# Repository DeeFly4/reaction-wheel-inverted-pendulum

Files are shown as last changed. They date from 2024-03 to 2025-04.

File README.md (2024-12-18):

# Reaction wheel inverted pendulum

This repository contains the code, schematics and the report for a school project course in Control Systems. The design, implementation and tuning of the controller was done by me with Arduino code. Much of the other parts of the project was handled by others in the group including design and creation of the physical parts as well as simulations in Matlab.

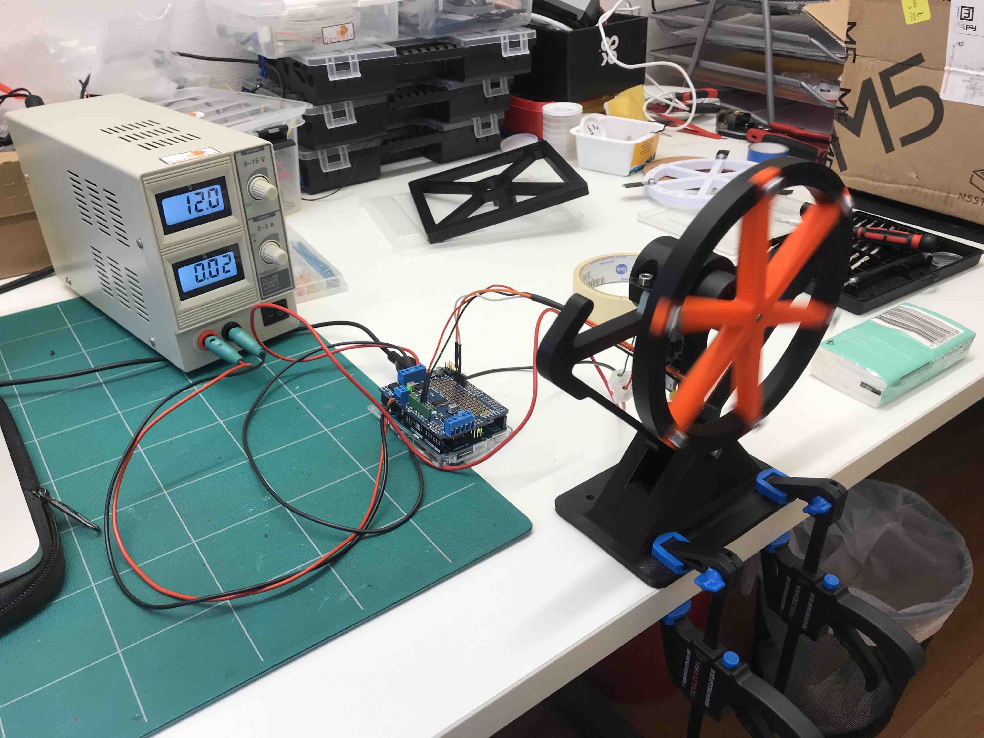
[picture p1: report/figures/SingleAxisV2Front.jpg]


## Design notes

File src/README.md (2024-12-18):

# Requirements
Both projects are Arduino code using PlatformIO. It can not be run through the standard Arduino IDE. Instead you will need to use Microsoft's Visual Studio Code with the PlatformIO extension.

## PlatformIO
1. Open VSCode Extension Manager
2. Search for offical PlatformIO IDE extension
3. Install PlatformIO IDE

For further info on PlatformIO, go to their website https://platformio.org/

# Running the code
Open either PlatformIO project, balance or imu, in a separate window. This will build the project locally to make sure all dependencies are installed according to the project's platformio.ini file. The standard Arduino code with setup() and loop() functions will be located in the files called main.cpp. In these files you will find further instructions to make sure the wiring is correct. Make sure to also follow the instructions in the serial monitor to start the program correctly.

The project must then be uploaded to the Arduino. This can be done by pressing the upload button at the bottom tool bar in VSCode.

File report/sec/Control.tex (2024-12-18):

Two control strategies were considered, PID-control and an observer-based controller using LQG.

\subsection{PID-control}
The PID controller continuously reads the current output signal $\theta_b(t)$ and compares it to the reference signal $r(t)$ to calculate the current error $e(t) = r(t) - \theta_b(t)$. The control signal $u(t)$ is then decided according to

\begin{equation}\label{eq:PIDcont}
    u(t) = K_P e(t) + K_I \int_0^t e(\tau) \ d\tau + K_D \frac{d}{dt}e(t),
\end{equation}

\noindent
where the control parameters $K_P$, $K_I$ and $K_D$ are predetermined. Since the objective is to balance a pendulum, i.e., make $\theta_b=0$. The reference will therefore be set to $r=0$. Since the controller has to be discretized in the implementation the integral is replaced by a sum and the derivative by a difference quotient. If the output signal is read at time intervals of $\Delta t$ we get

\begin{equation}\label{eq:PIDdisc}
    \begin{gathered}
        u(t) = K_Pe(t) + K_I \sum_{k=0}^N [e(k\Delta t)\Delta t] + K_D \frac{e(t) - e(t-\Delta t)}{\Delta t}, \\
        t = N\Delta t,
    \end{gathered}
\end{equation}

\noindent
for the number of samples $N$. The sampling time $\Delta t$ can be baked into the parameters $K_I$ and $K_D$ leading to fewer calculations in the code implementation. For ease of reading we let 

\begin{equation}
    \begin{gathered}
        I(t) = \sum_{k=0}^N [e(k\Delta t)\Delta t], \\
        D(t) = \frac{e(t) - e(t-\Delta t)}{\Delta t}, \\
        t = N\Delta t.
    \end{gathered}
\end{equation}

\subsection{Additions to the PID controller}
The first addition is adjusting the reference signal based on the current error. If the reference is moved further away from the current output the error will be larger and the controller will have a stronger response. For an angle increment of $\Delta\theta$ the updated reference angle $r(t+\Delta t)$ will be

\begin{equation}\label{eq:ref-adjustment}
    r(t+\Delta t) =
    \begin{cases}
        r(t) + \Delta\theta, \ \ \ e(t) > 0. \\
        r(t) - \Delta\theta, \ \ \ e(t) < 0.
    \end{cases}
\end{equation}

\noindent
This will have the most significant impact on the integral part of the controller. The increment value should be relatively small, especially with a quick sample time, otherwise the controller may not be able to catch up. This can be beneficial if you want especially the integral part to grow quickly. We also introduce an integral saturation $I_{\text{max}}$, making the sum $I(t)$ capped to $\pm I_{\text{max}}$.
\\\\
Another addition to the PID controller was motor feedback. This was achieved by having the control signal feedback into itself. With a discretized controller this becomes quite simple by introducing a fourth control parameter, $K_C$, and adding the term $K_Cu(t-\Delta t)$ to equation \eqref{eq:PIDdisc}, giving

\begin{equation}\label{eq:PIDCdisc}
    u(t) = K_P e(t) + K_I I(t) + K_D D(t) + K_C u(t-\Delta t).
\end{equation}

\subsection{LQG control}
First, we introduce independent disturbance and noise processes $\mathbf{w}_k$ and $\mathbf{v
}_k$ into the discrete-time system from \eqref{eq:ss-disc} to get

\begin{equation}
    \begin{gathered}
        \mathbf{x}_{k+1} = A_d\mathbf{x}_k + B_du_k + \mathbf{w}_k, \\
        \mathbf{y}_k = C\mathbf{x}_k + \mathbf{v}_k.
    \end{gathered}
\end{equation}

\noindent
Let both processes be white Gaussian noise with covariance matrices $V$ and $W$ respectively. By introducing a Kalman filter and state feedback we form the control equations

\begin{equation}\label{eq:LQG}
    \begin{gathered}
        \hat{\mathbf{x}}_{k+1} = A_d\hat{\mathbf{x}}_k + B_du_k + L(\mathbf{y}_k - C\hat{\mathbf{x}}_k),\\
        u_k = K\hat{\mathbf{x}}_k,
    \end{gathered}
\end{equation}

\noindent
where $\hat{\mathbf{x}}_k$ is the estimated state vector. In order to use equation \eqref{eq:LQG}, both matrices $K$ and $L$ need to be determined. They were determined by solving the linear-quadratic-Gaussian (LQG) optimal control problem. The feedback gain $K$ is chosen such that it minimizes the cost function

\begin{equation}\label{eq:LQG-cost}
    J(u) = \sum_{k=1}^\infty \mathbf{x}_k^T Q \mathbf{x}_k + u_k^T R u_k,
\end{equation}

\noindent
for some weight matrices $Q$ and $R$. Both the feedback gain $K$ and the Kalman gain $L$ can be obtained by solving their respective algebraic Riccati equations. This was done in Matlab using the commands \texttt{dlqr} and \texttt{dlqe}, which determines the $K$ and $L$ matrices respectively. For \texttt{dlqr}, the weight matrices had to be chosen, which was done by experimenting with different penalties. For \texttt{dlqe}, the covariance matrix for the measurement noise could be estimated using measured data. Estimating the covariance matrix for the noise affecting the states is difficult, and therefore an identity matrix is used instead.

\subsection{Motor limitations}
Most of the components used were off-the-shelf components, that were available at the university. This was a limiting factor, especially in terms of motors. A weak motor that provides low torque, puts a restriction on the maximum recovery angle. By analyzing the system statically at some tilt angle $\alpha$, we can calculate the motor torque necessary to cancel out the torque $T_O$ in the pivot point due to the gravitational force on the system. The torque $T_O$ can be calculated as

\begin{equation}\label{eq:tau}
    T_O = (m_b^*+m_w)gl \sin \alpha,
\end{equation}

\noindent
where $m_b^*$ is the mass of the pendulum body and the motor being considered. This equation was used to estimate motor requirements depending on the mass of the motor and desired recovery angles. The torque $T_O$ can be seen as the bare minimum to recover from $\alpha$. In practice, much higher torque is required if the pendulum is to also accelerate towards the equilibrium. Note also that the pendulum will not be still when at this angle $\alpha$. It will have fallen there and thus have a non-zero angular velocity, requiring an even higher torque.

\subsection{Sampling limitations}
Apart from torque generation in the motors, the sampling time is also an important factor. In these types of unstable (open loop) systems a quick sampling rate is of critical importance in order to recover from disturbances before it is too late. Although a fast sampling rate is desired, it is limited by the hardware. The most limiting factor for the sampling time was the IMU, which outputs data at 100 Hz\cite{IMU-datasheet} i.e. a sample time of 10 ms.

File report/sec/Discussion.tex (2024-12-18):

Our supervisor said during a meeting that "There are two ways of solving a control problem. Either, one designs the system and actively chooses which components are to be used, or one is given a complete system and has to do a lot more work on control modelling and algorithms."

\subsection{Limitations in the simulation}
There were a number of limitations in the simulation that has to be addressed. First of all, the simulation uses the linearized model in \eqref{eq:state-space}. This does not completely represent the reality of the dynamics of the single axis setup. However, since the working range of the angle of the system is only a couple of degrees, it was reasonable to use the linearized model. Second of all, many of the parameters used in the model were approximated. The moments of inertia were all derived using standard formulas and could have been more accurate. Another example is the friction coefficient, which was taken from \cite{cubli-planar}. Although there are a number of limitations to the simulation, the purpose of it was not to get a working controller that could be directly applied to the real model, but instead to see how a PID controller compares to a LQG controller, and which parameters are important.

\subsection{Interpreting the simulations}
As seen in Figures~\ref{fig:PIDGraph} and \ref{fig:LQGGraph}, both controllers could stabilize the system with the given set of parameters. They could also handle an impulse disturbance of $0.5\degree$. When comparing the two controllers, one instantly notes the smoother response of the LQG controller. However, the LQG is highly dependent on a good model of the system and to what extent our model and parameters are sufficient, will not be answered in this paper, since a LQG controller was not implemented in the real system. Both controllers in the simulation used a sampling time of 15 ms. This was done in order to insure that the sampling time was not impossible to meet.
\\\\
As mentioned in Table~\ref{table:ParamSig}, the most significant parameters were the sampling time, the maximum torque that the motor can generate and the length to center of mass from the pivot point. This is reasonable since a longer length to the center of mass will increase the torque required cancel the gravitational force. The motor torque is also important to counter the torque generated by the body itself. It is also reasonable that the sampling time is significant, since  even a small change in angle will have large effect on the necessary torque to counter the fall and the change in angle should be measured as fast as possible. Also, the mass of the frame and the radius of the wheel, seemed less important. This is likely due to the fact that the mass of the frame is already low, and the same applies to the length to center of mass. The same applies to the friction coefficient and the mass of the wheel, which both already had low values. It is important to note that this observation was only done qualitatively, since the simulation is based on approximations. The purpose was to observe the trends mentioned above rather than finding the exact parameters that can be handled. With this said, it would be recommended to initially lower the sampling time, increase the maximum torque and diminish the length to center of mass, before changing anything else. 
\\\\
Comparing the PID parameters in Table~\ref{table:PIDParameters} with the real ones, one notices a large difference. This is because of a number of reasons. One being that the control signal is very different when comparing Figure~\ref{fig:PIDGraph} with Figure~\ref{fig:physical-balance}, since the simulation input signal is in ampere and the code for the real process is the velocity for the wheel. Also, the simulation inputs angles in radiance, while the real process inputs angles in degrees. Another reason why the PID parameters differ, is because the physical parameters differ between the simulation and the real process. This is true, since the real setup used is not the same as in Figure~\ref{fig:cubli_planar_diagram}, which is the structure simulated. Also, most parameters were identified and can differ from the real physical parameters.

\subsection{Tuning the PID controller on the single axis setup}
The PID controller was tuned through trial and error with the help of some intuitive reasoning. Most of the early tuning was done with only PD-control. Due to the system's instability there can be no steady state error, leading us to believe no integral action should be used. But these ideas proved to be flawed.
\\\\
Firstly, while it is true that we may want to ease up on the torque when the pendulum is already on its way up, that does not mean to lower the control signal. Remember that the control signal is (roughly) proportional to speed so a lower control signal actually means decelerating the wheel. If the wheel decelerates while the pendulum is rising the effect is a torque going the opposite way, sending the pendulum back down. So a too large $K_D$ may hurt the balancing.
\\\\
Secondly, by introducing integral action we can get the desired behavior of increasing the speed, which maintains torque, even when the pendulum is rising. The introduction of integral action is likely also why the control signal oscillates around a positive base speed instead of 0. It is then important to have integral action that reacts quickly, but does not grow too large. This is why setting $I_{\text{max}} < u_{\text{max}}$ and adding reference adjustment eventually led to the best results. Another advantage of reference adjustment is that it allows the process to find its own equilibrium. A very interesting example of this can be found in \cite{LEGO-video} at 11:25. If there is a discrepancy between what the IMU registers as $0\degree$ and the physical equilibrium, it could be hard to achieve balance if always controlling to $r=0$. This explains the results seen in Figure~\ref{fig:physical-balance}. The reference adjustment turned out to be crucial for this reason.

\subsection{IMU signal}
Surprisingly, when measuring the output angle from the IMU we could not detect any noise at all (Figure~\ref{fig:imu_angle}). Despite this the raw data readings from the gyrometer were very noisy (Figure \ref{fig:imu_gyro}). This is problematic if implementing state feedback in the microcontroller. A good observer would then be needed, consequently requiring a more accurate model to develop this observer with the help of simulations. An alternate way of estimating $\dot\theta_b$ is of course with a difference quotient, as in the discretized PID controller. We considered using the gyrometer readings as a more accurate estimate of the derivative even with PID control, but after discovering the noisiness we decided against it.

\subsection{Weight reduction}
In cases where more time is available, the final design can be developed through several iterations. For this project, time was sufficient for designing a single axis setup as a pilot study for the actual cube. While the thickness of the cube frame was heavily reduced, compared to the previous prototype, at points where it could be done, after printing it was concluded that the thickness could have been reduced even more in order to save weight. Although, the group is concerned if such a weight reduction would be enough for the motors to be strong enough to balance the cube. The components on their own also contributed to the total weight. With this in mind, even stronger motors would almost certainly be needed if the cube is to be driven by a large battery like in this case.

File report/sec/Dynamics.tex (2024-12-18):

For both the cube and the single axis setup, the system dynamics can be analyzed in one plane only, provided the reaction wheel is parallel to that plane. In that case, the system is effectively an inverted pendulum constrained to one axis around a pivot point. When doing the mathematical analysis, we focused on the single axis setup as in Figure~\ref{fig:cubli_planar_diagram},

\begin{figure}[H]
    \centering
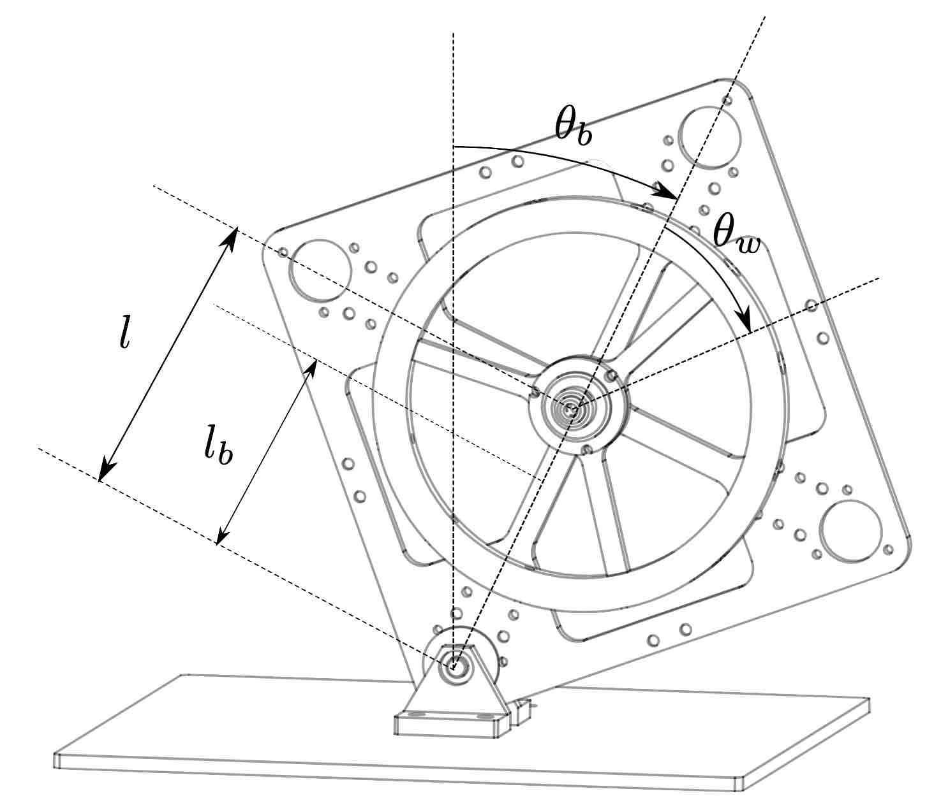
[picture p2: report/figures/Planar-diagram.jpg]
    
    \caption{Diagram of single axis setup from \cite{cubli-planar}.}
    \label{fig:cubli_planar_diagram}
\end{figure}

\noindent
where $\theta_b$ is the tilt angle of the pendulum body and $\theta_w$ is the angle of the wheel with respect to the body. The distance between the motor and the pivot point $O$ is denoted by $l$ whereas $l_b$ is the distance between the pendulum body's center of mass and $O$. Due to the symmetry of our prototype we assumed that $l = l_b$. We also assumed zero friction in the pivot point due to the use of a ball bearing. With these assumptions, we can modify the system of equations from \cite{cubli-planar} to get

\begin{equation}\label{eq:system}
    \begin{gathered}
        \ddot\theta_b = \frac{(m_b + m_w)gl\sin\theta_b - T_m +C_w\dot\theta_w}{I_b + m_wl^2}, \\
        \ddot\theta_w = \frac{(I_b + I_w + m_wl^2) \left( T_m - C_w\dot\theta_w \right)}{I_w(I_b + m_wl^2)} \\- \frac{(m_b + m_w)gl\sin\theta_b}{I_b + m_wl^2},
    \end{gathered}
\end{equation}

\noindent
where $m_b$ is the mass of the structure and the motor, $m_w$ is the mass of the reaction wheel, $T_m$ is the motor torque, $C_w$ is the dynamic friction coefficient of the wheel. $I_w$, $I_b$ are the moments of inertia of the wheel around its rotational axis and the pendulum body around $O$ respectively.

\subsection{Motor dynamics}
The motors used were initially simple brushed DC motors whose relation between torque $T_m$ and current $i$ drawn by the motor can be described as

\begin{equation}
    T_m = K_mi,
\end{equation}

\noindent
where $K_m$ is the torque constant. We can hence describe the acceleration of the reaction wheel as

\begin{equation}\label{eq:motor}
    \ddot\theta_w = \frac{K_m i - C_w\dot\theta_w}{I_w}.
\end{equation}

\subsection{State-space model}
We can now combine \eqref{eq:system} and \eqref{eq:motor} to get a full model that accounts for the current $i$. By using the approximation of small angles, $\sin\theta \approx \theta$, the system of equations becomes linear. The state variables are chosen as $\mathbf{x} = [\theta_b \ \dot\theta_b \ \dot\theta_w]^T$. Linearizing around $[0 \ 0 \ 0]^T$ gives

\begin{equation}\label{eq:state-space}  
    \begin{gathered}
        \dot{\mathbf{x}} = A\mathbf{x} + Bu, \\
        \mathbf{y} = C\mathbf{x},
    \end{gathered}
\end{equation}

\noindent
where

\begin{equation}\label{eq:ss-matrices}
    \begin{gathered}
        A =
        \begin{bmatrix}
            0 & 1 & 0 \\
            \frac{(m_b+m_w)gl}{I_b+m_wl^2} & 0 & \frac{C_w}{I_b+m_wl^2} \\
            -\frac{(m_b+m_w)gl}{I_b+m_wl^2} & 0 & -\frac{C_w(I_b+I_w+m_wl^2)}{I_w(I_b+m_wl^2)}
        \end{bmatrix}
        , \\
        B =
        \begin{bmatrix}
            0 \\
            -\frac{K_m}{I_b + m_wl^2} \\
            \frac{K_m(I_b+I_w+m_wl^2)}{I_w(I_b+m_wl^2)}
        \end{bmatrix}
        \text{ and } C =
        \begin{bmatrix}
            1 & 0 & 0 \\
            0 & 1 & 0 
        \end{bmatrix},
    \end{gathered}
\end{equation}

\noindent
where the control signal $u$ is the current $i$ and the output signal $\mathbf{y}$ is both $\theta_b$ and $\dot\theta_b$. The goal is to control only $\theta_b$ and stabilize it around 0, but the angular velocity $\dot\theta_b$ will also be directly readable from sensor data.
\\\\
The state-space model was then discretized using zero-order hold to get the discrete-time model

\begin{equation}\label{eq:ss-disc}
    \begin{gathered}
        \mathbf{x}_{k+1} = A_d\mathbf{x}_k + B_du_k,\\
        \mathbf{y}_k = C\mathbf{x}_k,
    \end{gathered}
\end{equation}

\noindent
where $A_d$ and $B_d$ are the discrete-time counterparts to $A$ and $B$.

\subsection{Parameter identification}
To simulate the state-space model, the physical parameters had to be identified. $I_b$ was calculated with

\begin{equation}\label{eq:Ib}
    I_{b} = \frac{s_{f}^2}{6}m_{f} + \frac{r_{m}^2}{2}m_{m} + (m_{f} + m_{m})l^2,
\end{equation}

\noindent
where $s_{f}$ is the side length of the frame, $r_{m}$ is the radius of the motor, $m_{f}$ is the mass of the frame and $m_{m}$ is the mass of the motor. $I_w$ was calculated with

\begin{equation}\label{eq:Iw}
    I_{w} = \frac{1}{2}m_{w}(r_{\text{outer}}+r_{\text{inner}})^2
\end{equation}

\noindent
where $r_{\text{outer}}$ is the radius of the wheel and $r_{\text{inner}}$ is the radius to the inner edge of the wheel. The maximum torque of the motor can be found in \cite{motor-datasheet}. The torque constant $K_{m}$ can also be calculated from the data sheet, using the equation

\begin{equation}\label{eq:Km}
    K_{m} = \frac{T_{2} - T_{1}}{i_{2} - i_{1}},
\end{equation}

\noindent
where the torques $T_1, T_2$ and currents $i_1, i_2$ were chosen at two different points.

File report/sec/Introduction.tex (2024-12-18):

The goal of this project is to explore the possibility of making a cube balance on its edges by utilizing reaction wheels. Additionally, there are some key areas that were focused on in this project in order for the participants to gather additional experience. These are the following:

\begin{itemize}
    \item Working with a overarching system perspective.
    \item Producing prototypes by means of 3D printing.
    \item Writing a functioning control algorithm tailored to the problem. 
    \item Creating a working program for the entire system.
\end{itemize}

\noindent
The project was divided into three subtasks where the first was to balance an inverted pendulum on a single axis setup, the second was to balance a cube on an edge and the third was to have the cube rise to an edge from rest.

\subsection{Previous work}
This project has been a replica of the work done by M. Gajamohan et. al\cite{cubli-planar}. Their work has shown that it is possible to make a cube balance using reaction wheels and it also a source of information in which the group could to some extent find relevant equations for calculations. However, it must be mentioned that a Google search also indicates Gajamohan et al. are not the only group to have done this kind of project. Other sources of inspiration are the many open source projects from ReM-RC\cite{remrc} and this YouTube video\cite{LEGO-video}.

\subsection{Concept of reaction wheels}
Reaction wheels are a motor-controlled variant of flywheels, i.e. free spinning wheels used to store rotational energy by conserving angular momentum. When the rotational speed of the wheel changes, the body its attached to will counter-rotate due to the conservation of angular momentum. Note that rotation of the body can only happen during torque, meaning that accelerating a still wheel has the same effect as braking an already spinning wheel. By attaching a motor to the fly wheel these torques can be controlled, creating a reaction wheel. One of the most common applications of reaction wheels is in spacecrafts and satellites, where multiple wheels are used to control and stabilize the orientation.

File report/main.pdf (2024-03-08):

# Self-balancing cube

# Daniel Holm¹ Rasmus Kalvenes² Jonathan Vesterlund³ Gustaf Walden´

4

Project Advisor: Olle Kjellqvist⁵

1da5838ho-s@student.lu.se | 2ra0820ka-s@student.lu.se | 3jo2583ve-s@student.lu.se
| 4gu6615wa-s@student.lu.se

Abstract: The aim of this project was to make a cube balance on an edge, or even a corner

if time allows it. This would be done with reaction wheels inside the structure. Besides this,

the project also focused on working from a system design perspective, including 3D-printing

and selecting electrical components. Using a PID controller with some additions, the group

successfully balanced a single axis variant of the problem. A functioning LQG controller was

also implemented in simulations of the problem. The learning experience was great. The most

significant factors for achieving balance were sampling time, motor strength and pendulum length.

A cube structure was created, but could not be made to balance due to time constraints and the

factors mentioned.

# 1. Introduction

The goal of this project is to explore the possibility of mak-

ing a cube balance on its edges by utilizing reaction wheels.

Additionally, there are some key areas that were focused on

in this project in order for the participants to gather additional

experience. These are the following:

- Working with a overarching system perspective.
- Producing prototypes by means of 3D printing.
- Writing a functioning control algorithm tailored to the

problem.

- Creating a working program for the entire system.

The project was divided into three subtasks where the first was

to balance an inverted pendulum on a single axis setup, the

second was to balance a cube on an edge and the third was to

have the cube rise to an edge from rest.

# 1.1 Previous work

This project has been a replica of the work done by M. Ga-

jamohan et. al[5]. Their work has shown that it is possible

to make a cube balance using reaction wheels and it also a

source of information in which the group could to some extent

find relevant equations for calculations. However, it must be

mentioned that a Google search also indicates Gajamohan et

al. are not the only group to have done this kind of project.

Other sources of inspiration are the many open source projects

from ReM-RC[7] and this YouTube video[4].

# 1.2 Concept of reaction wheels

Reaction wheels are a motor-controlled variant of flywheels,

i.e. free spinning wheels used to store rotational energy by

conserving angular momentum. When the rotational speed

of the wheel changes, the body its attached to will counter-

rotate due to the conservation of angular momentum. Note that rotation of the body can only happen during torque, meaning

that accelerating a still wheel has the same effect as braking an

already spinning wheel. By attaching a motor to the fly wheel

these torques can be controlled, creating a reaction wheel.

One of the most common applications of reaction wheels is in

spacecrafts and satellites, where multiple wheels are used to

control and stabilize the orientation.

# 2. Physical setups

Besides reaction wheels, one for each axis to be balanced

around, there are several other components. One motor to drive

each reaction wheel and to control the motors an Arduino UNO

R3[3] was used. In addition, an Adafruit Motor Shield v2.0[1]

was used to control the motors. The shield has the capability

to distribute current to the motors of the system from the

battery. Combined with Adafruit’s library[2], the shield uses

pulse-width modulation (PWM) to control speed and direction

of DC motors. This was needed since it allows for a higher

voltage and stronger current than what the Arduino can supply.

The microcontroller reads the measurements from an inertial

measurement unit (IMU) which calculates the current angle

of the system. The IMU used was the BNO055 from Bosch

Sensortec[8] with the help of Adafruit’s library[IMU-lib].

# 2.1 Single axis setup

In order to get a better understanding of reaction wheel bal-

ancing a single axis setup was designed and 3D-printed. This

setup can be seen in Figure 1. The single axis setup was later

modified and improved. The full assembly, including elec-

tronic components can be seen in figure 2. Despite it being a

simple structure, it has the benefit of easy access to port. The

microcontroller was not attached to the structure, it laid flat

on the table. A prototype build like this allowed us to detect

which components are sufficient for the end goal.

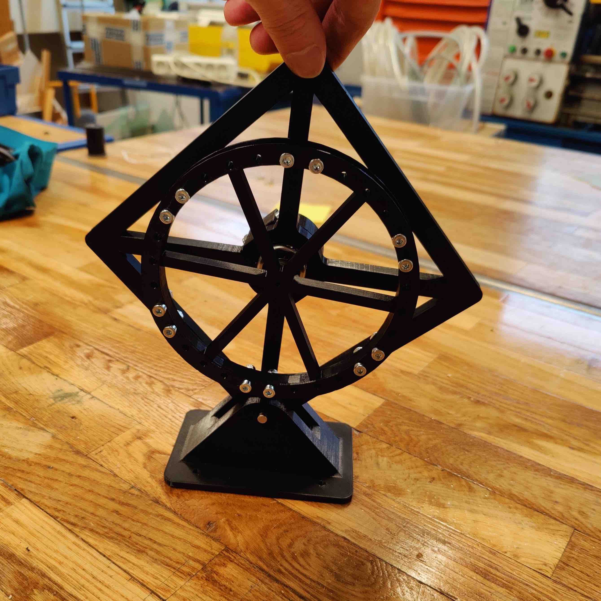
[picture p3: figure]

Figure 1. The first version of the single axis setup


Figure 2. The second version of the single axis setup, with electri-

cal components

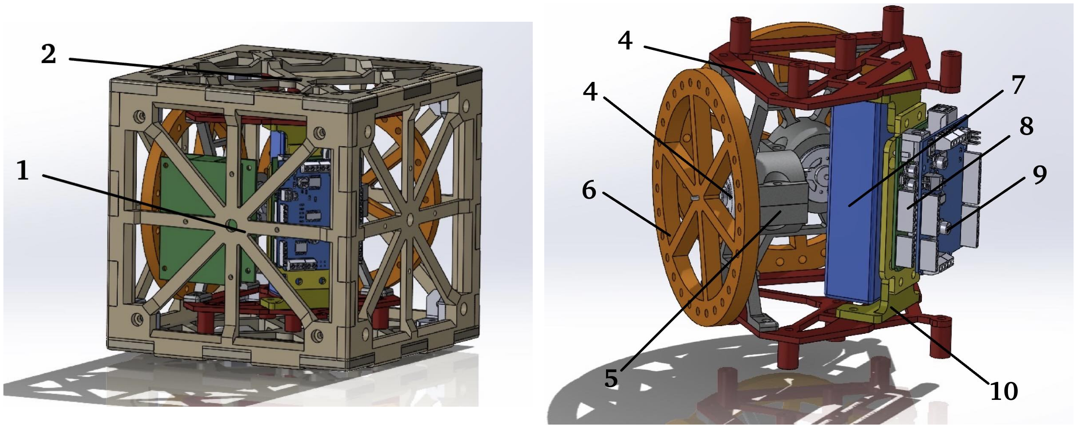
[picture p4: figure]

Figure 3. The components in the system numbered.

# 2.2 The cube

Designing the structure for the cube proved to be a lot more

difficult and time consuming than expected. The intricate de-

sign demanded things to be decided based on assumptions,

which later turned out to be incorrect. Some parts had to be

redesigned multiple times. Some parts, e.g. four sides of the

cube, were made identical to make the printing process less

difficult. Other parts, engine mounts among them, were made

symmetrical for the same reason. An advantage of having mul-

tiple identical parts is that if one part fails, it can potentially

be replaced by another. While the replacement part is being

printed, a side of the cube that is not critical when testing can

be relocated into the critical position. The design of the cube

can be seen in Figure 3 with the parts named in Table 1.

Component | Number
Cube, side | 1
Cube, top and bottom | 2
Mounting plate | 3
DC motor | 4
Motor holder | 5
Reaction wheel | 6
Battery | 7
Arduino | 8
Arduino Shield | 9
Electronics holder | 10

Table 1. The components in the system.

# 3. System dynamics

For both the cube and the single axis setup, the system dynam-

ics can be analyzed in one plane only, provided the reaction

wheel is parallel to that plane. In that case, the system is ef-

fectively an inverted pendulum constrained to one axis around

a pivot point. When doing the mathematical analysis, we fo-

cused on the single axis setup as in Figure 4,


Figure 4. Diagram of single axis setup from [5].

where θb is the tilt angle of the pendulum body and θw is

the angle of the wheel with respect to the body. The distance

between the motor and the pivot point O is denoted by l

whereaslb is the distance between the pendulum body’s center

of mass and O. Due to the symmetry of our prototype we

assumed that l = lb. We also assumed zero friction in the pivot

point due to the use of a ball bearing. With these assumptions,

we can modify the system of equations from [5] to get

θ¥
b =

(mb + mw)gl sin θb − Tm + Cwθ¤w

## Ib + mwl

2

,

θ¥w =

## (Ib + Iw + mwl

2
)

Tm − Cwθ¤w

## Iw (Ib + mwl

2
)

−

(mb + mw)gl sin θb

## Ib + mwl

2

,

(1)

where mb is the mass of the structure and the motor, mw is

the mass of the reaction wheel, Tm is the motor torque, Cw is

the dynamic friction coefficient of the wheel. Iw, Ib are the moments of inertia of the wheel around its rotational axis and

the pendulum body around O respectively.

# 3.1 Motor dynamics

The motors used were initially simple brushed DC motors

whose relation between torque Tm and current i drawn by the

motor can be described as

Tm = Kmi, | (2)

where Km is the torque constant. We can hence describe the

acceleration of the reaction wheel as

θ¥w =

## Kmi − Cwθ¤w

Iw

. | (3)

# 3.2 State-space model

We can now combine (1) and (3) to get a full model that

accounts for the current i. By using the approximation of small

angles, sin θ ≈ θ, the system of equations becomes linear. The

state variables are chosen as x = [θb θ¤

b θ¤w]
T
| . Linearizing

around [0 0 0]

T gives

x¤ = Ax + Bu,

y = Cx,

| (4)

where

A =

0 | 1 | 0

(mb+mw )gl

Ib+mwl

2 | 0 | Cw Ib+mwl

2
−

(mb+mw )gl

Ib+mwl

2 | 0 | − Cw (Ib+Iw+mwl

2
)
| | Iw (Ib+mwl

2
)

,

B =

0
−

Km
Ib+mwl

2
Km (Ib+Iw+mwl

2
)

Iw (Ib+mwl

2
)

## and C =

1 | 0 | 0
0 | 1 | 0
,

(5)

where the control signal u is the current i and the output signal

## y is both θb and θ¤

b. The goal is to control only θb and stabilize

it around 0, but the angular velocity θ¤
b will also be directly

readable from sensor data.

The state-space model was then discretized using zero-order

hold to get the discrete-time model

xk+1 = Adxk + Bduk,

yk = Cxk,

(6)

where Ad and Bd are the discrete-time counterparts to A and

B.

# 3.3 Parameter identification

To simulate the state-space model, the physical parameters

had to be identified. Ib was calculated with

Ib =

s

2
f
6

m f +

r

2

m
2

mm + (m f + mm)l

2
, | (7)

where sf

is the side length of the frame, rm is the radius of

the motor, m f

is the mass of the frame and mm is the mass of

the motor. Iw was calculated with

Iw =

1

2

mw (router + rinner)

2
(8)

where router is the radius of the wheel and rinner is the radius

to the inner edge of the wheel. The maximum torque of the

motor can be found in [6]. The torque constant Km can also

be calculated from the data sheet, using the equation

Km =

T2 − T1

i2 − i1

, | (9)

where the torques T1, T2 and currents i1, i2 were chosen at two

different points.

# 4. Controlling the process

Two control strategies were considered, PID-control and an

observer-based controller using LQG.

# 4.1 PID-control

The PID controller continuously reads the current output sig-

nal θb (t) and compares it to the reference signal r(t) to cal-

culate the current error e(t) = r(t) − θb (t). The control signal

u(t) is then decided according to

u(t) = KPe(t) + KI

∫ t

0

e(τ) dτ + KD

d

dt

e(t), | (10)

where the control parameters KP, KI and KD are predeter-

mined. Since the objective is to balance a pendulum, i.e., make

θb = 0. The reference will therefore be set to r = 0. Since the

controller has to be discretized in the implementation the in-

tegral is replaced by a sum and the derivative by a difference

quotient. If the output signal is read at time intervals of Δt we

## get

u(t) = KPe(t) + KI

∑︁

N

k=0

# [e(kΔt)Δt] + KD

### e(t) − e(t − Δt)

Δt

,

t = NΔt,
(11)

for the number of samples N. The sampling time Δt can be

baked into the parameters KI and KD leading to fewer cal-

culations in the code implementation. For ease of reading we

## let

I(t) =

∑︁

N

k=0

[e(kΔt)Δt],

D(t) =

### e(t) − e(t − Δt)

Δt

,

t = NΔt.

(12)

# 4.2 Additions to the PID controller

The first addition is adjusting the reference signal based on

the current error. If the reference is moved further away from

the current output the error will be larger and the controller

will have a stronger response. For an angle increment of Δθ

the updated reference angle r(t + Δt) will be

### r(t + Δt) =

(
r(t) + Δθ, | e(t) > 0.
r(t) − Δθ, | e(t) < 0.

(13)

This will have the most significant impact on the integral part

of the controller. The increment value should be relatively

small, especially with a quick sample time, otherwise the

controller may not be able to catch up. This can be beneficial

if you want especially the integral part to grow quickly. We

also introduce an integral saturation Imax, making the sum

I(t) capped to ±Imax.

Another addition to the PID controller was motor feedback.

This was achieved by having the control signal feedback into

itself. With a discretized controller this becomes quite simple

by introducing a fourth control parameter, KC, and adding the

term KCu(t − Δt) to equation (11), giving

## u(t) = KPe(t) + KI I(t) + KD D(t) + KCu(t − Δt). (14)

# 4.3 LQG control

First, we introduce independent disturbance and noise pro-

cesses wk and vk into the discrete-time system from (6) to

## get

xk+1 = Adxk + Bduk + wk,

yk = Cxk + vk .

(15)

Let both processes be white Gaussian noise with covariance

matrices V and W respectively. By introducing a Kalman filter

and state feedback we form the control equations

xˆ k+1 = Adxˆ k + Bduk + L(yk − Cxˆ k),

uk = Kxˆ k,

(16)

where xˆ k is the estimated state vector. In order to use equation

(16), both matrices K and L need to be determined. They were

determined by solving the linear-quadratic-Gaussian (LQG)

optimal control problem. The feedback gain K is chosen such

that it minimizes the cost function

J (u) =

∑︁∞

k=1

x

T
k Qxk + u

T
k Ruk, | (17)

for some weight matrices Q and R. Both the feedback gain

K and the Kalman gain L can be obtained by solving their

respective algebraic Riccati equations. This was done in Mat-

lab using the commands dlqr and dlqe, which determines

the K and L matrices respectively. For dlqr, the weight ma-

trices had to be chosen, which was done by experimenting

with different penalties. For dlqe, the covariance matrix for

the measurement noise could be estimated using measured

data. Estimating the covariance matrix for the noise affecting

the states is difficult, and therefore an identity matrix is used

instead.

# 4.4 Motor limitations

Most of the components used were off-the-shelf components,

that were available at the university. This was a limiting factor,

especially in terms of motors. A weak motor that provides low torque, puts a restriction on the maximum recovery angle. By

analyzing the system statically at some tilt angle α, we can

calculate the motor torque necessary to cancel out the torque

TO in the pivot point due to the gravitational force on the

system. The torque TO can be calculated as

## TO = (m

∗
b
+ mw)gl sin α, | (18)

where m

∗
b

is the mass of the pendulum body and the motor

being considered. This equation was used to estimate motor

requirements depending on the mass of the motor and desired

recovery angles. The torque TO can be seen as the bare min-

imum to recover from α. In practice, much higher torque is

required if the pendulum is to also accelerate towards the equi-

librium. Note also that the pendulum will not be still when at

this angle α. It will have fallen there and thus have a non-zero

angular velocity, requiring an even higher torque.

# 4.5 Sampling limitations

Apart from torque generation in the motors, the sampling time

is also an important factor. In these types of unstable (open

loop) systems a quick sampling rate is of critical importance

in order to recover from disturbances before it is too late.

Although a fast sampling rate is desired, it is limited by the

hardware. The most limiting factor for the sampling time was

the IMU, which outputs data at 100 Hz[8] i.e. a sample time

of 10 ms.

# 5. Results

# 5.1 Selecting the new motor

Out of the available off-the-shelf motors the L1491210[6]

from Micro Motors was selected. According to (18), it should

momentarily hold a tilt angle of 4°, which was more than twice

as powerful as the first motor used.

# 5.2 Physical parameters

The physical parameters were identified for the single axis

setup. These values were used for the simulations and can be

found in Table 2.

Parameter | Value
Ib | 2.1 · 10−3 kg · m2
Iw | 6.4 · 10−3 kg · m2
mb | 0.170 kg
mw | 0.076 kg
l | 0.093 m
Km | 0.5 Nm/A
Tmax | 0.015 Nm

Table 2. Parameters and their measured values.

The only parameter that was not identified was the friction

coefficient, Cw. Instead, the same value as the one in [5] was

## used, Cw = 5 · 10−5 kg · m2

- s

−1

# 5.3 Measurements from the IMU

The structure was tilted slowly from side to side while the

angle was measured at 10 ms intervals. The results can be

seen in Figure 5.

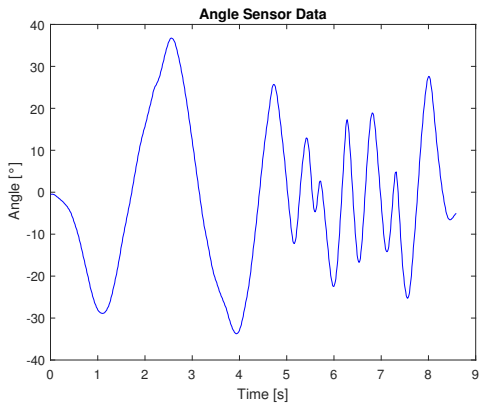
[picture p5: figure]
Time [s]; Angle [°]; Angle Sensor Data

Figure 5. Angle measurements from the IMU.

The structure was then laid still while the angular velocity

from the gyrometer was measured at 10 ms intervals. The

results can be seen in Figure 6.

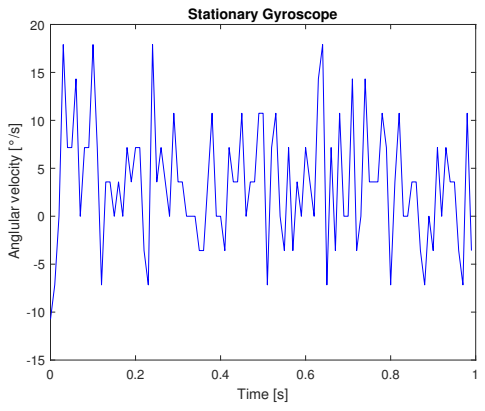
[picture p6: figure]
Time [s]; Anglular velocity [°/s]; Stationary Gyroscope

Figure 6. Angular velocity measurements from the IMU.

# 5.4 Simulations

The model in (4) and (5) was simulated using both a PID

controller and a LQG controller. The simulation results can be

seen in Figure 7 and Figure 8. For both simulations, a sample

time of 15 ms and a pulse disturbance of 0.5° was used.

The parameter settings for the discrete PID controller can

be seen in Table 3.

Parameter | Value
KP | 3
KI | 1
KD | 0.3

Table 3. The chosen PID parameters.

The optimal gain matrices K and L were calculated as

K =

6.0497 | 0.7365 | 0.0611
,

L =

1 | 0
14.0934 | 0.0825
0.8845 | 0.0048

(19)

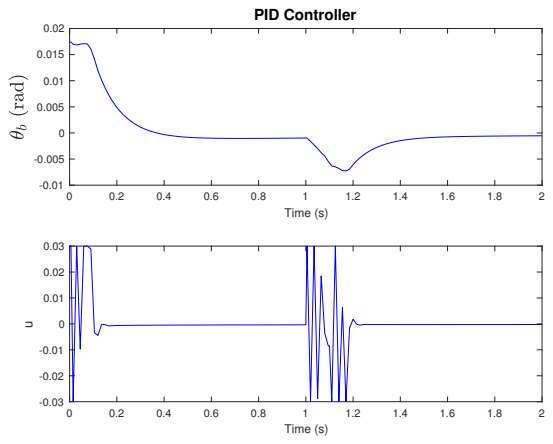
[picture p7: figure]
Time (s); PID Controller

Figure 7. Simulation of the single axis setup with a disturbance,

using the PID controller.

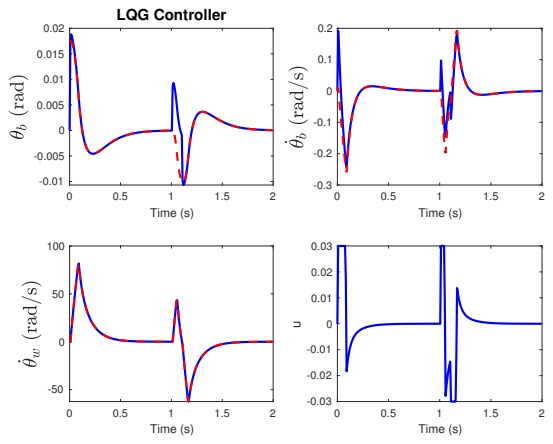
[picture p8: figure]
Time (s); LQG Controller

Figure 8. Simulation of the single axis setup with a disturbance,

using the LQG controller. The blue line represents the estimated

values and the red dashed line represents the values calculated from

the state-space model.

While experimenting with different parameter settings for the

simulation, we observed that some had a larger effect on the

system than others. By changing the parameters in the PID

simulation, with different factors, the parameters importance

could be observed. The observation was based on how high,

or low, of a factor a parameter could handle, before the sys-

tem achieved instability. Sampling time, maximum torque and

length to center of mass had the largest effect. This was fol-

lowed by the mass of the frame and the radius of the wheel. In

contrast, the system was still stable with a high friction coeffi-

cient and a low mass of the wheel. This qualitative observation

is summarized in Table 4.

Parameter | Factor | Importance
Δt | 1.2 | Very high
Tmax | 2.7
| −1 | High
l | 2.8 | High
mb | 4.5 | Medium
rw | 4.5
| −1 | Medium
mw | < 20−1 | Low
Cw | 40 | Low

Table 4. Parameters and their observed importance.

# 5.5 The physical setup

The discretized controller from (11) was implemented with a

sample time of 10 ms with the original DC motors given to

us. The motor was eventually swapped out to the new one[6].

After this, testing could begin again. This time the motor

feedback from (14) was also implemented. Experimenting

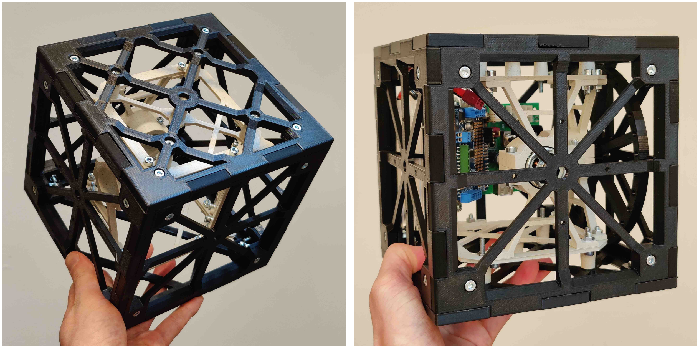
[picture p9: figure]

with PD-control and positive values of KC seemed promising

but balancing still proved difficult. In a last ditch effort a

new design for the pendulum body was made. The improved

structure can be seen in Figure 2.

After | some inspiration | from[4] the controller | now | made

use of integral action with a positive KI as well as reference

adjustment according to (13). KC was now chosen to be nega-

tive and relatively small. The idea was to slow down the wheel

over time when balancing. After some tuning stable balancing

was finally achieved with the following control parameters:

KP = 50, KI = 150, KD = 2.5, KC = −0.2,

Imax = 127, Δθ = 0.004.

(20)

Note that the control signal ranges between ±255 (where 255

is simply the max speed of the motor) and the output signal is

measured in degrees. The parameter Δθ is also in degrees. In

the code implementation, Δt was also baked into the constants

to reduce the amount of calculations. In Figure 9 we can see

roughly 15 seconds of balance using the control parameters

above. The sensor readings shown are spaced 50 ms apart, but

the controller still acted at the usual 10 ms intervals.

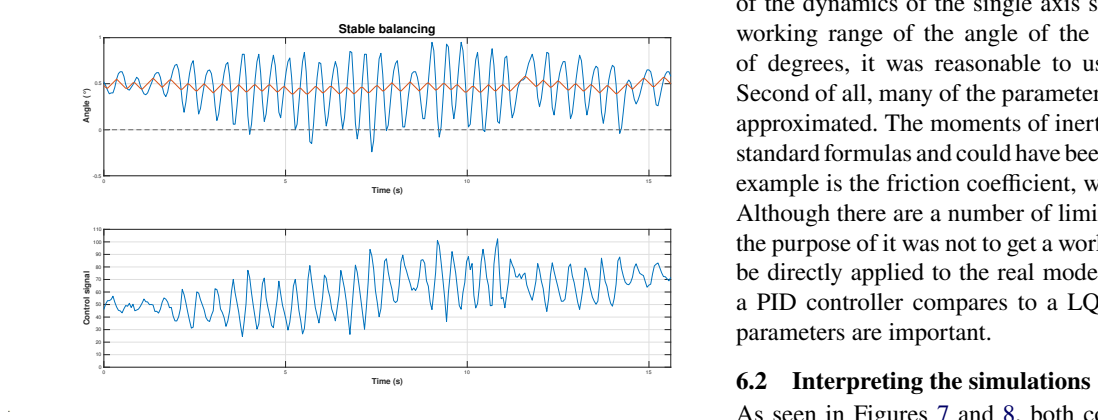
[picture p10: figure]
Time (s); Angle (°); Stable balancing; Control signal; parameters are important.; 6.2 Interpreting the simulations

Figure 9. Top graph: the measured angle θb is in blue and r is in

orange. Bottom graph is the control signal.

There are some key takeaways from this graph. Firstly, The

structure is not balancing around 0°. Instead, the reference

is oscillating slightly around 0.46°. The standard deviation

in error over this period was σe = 0.24°. Secondly, the con-

trol signal is also oscillating around a positive, non-zero speed.

Note that these 15 seconds were an excerpt from a longer

period of balancing. In reality, the structure could balance for

several minutes. The longest measured time balancing was

just shy of 37 minutes. It could also handle small disturbances

such as shaking the table and gently pushing the structure.

# 5.6 The cube

The physical model can be seen in Figure 10. The printed parts,

structural screws and nuts had a total mass of 587 grams. The

scale that was used had an upper limit of 1 kg, which the cube

exceeded with the rest of the internal components assembled.

Figure 10. The printed cube with and without components

# 6. Discussion

Our supervisor said during a meeting that ”There are two ways

of solving a control problem. Either, one designs the system

and actively chooses which components are to be used, or one

is given a complete system and has to do a lot more work on

control modelling and algorithms.”

# 6.1 Limitations in the simulation

There were a number of limitations in the simulation that has

to be addressed. First of all, the simulation uses the linearized

model in (4). This does not completely represent the reality

of the dynamics of the single axis setup. However, since the

working range of the angle of the system is only a couple

of degrees, it was reasonable to use the linearized model.

Second of all, many of the parameters used in the model were

approximated. The moments of inertia were all derived using

standard formulas and could have been more accurate. Another

example is the friction coefficient, which was taken from [5].

Although there are a number of limitations to the simulation,

the purpose of it was not to get a working controller that could

be directly applied to the real model, but instead to see how

a PID controller compares to a LQG controller, and which

As seen in Figures 7 and 8, both controllers could stabilize

the system with the given set of parameters. They could also

handle an impulse disturbance of 0.5°. When comparing the two controllers, one instantly notes the smoother response of

the LQG controller. However, the LQG is highly dependent

on a good model of the system and to what extent our model

and parameters are sufficient, will not be answered in this

paper, since a LQG controller was not implemented in the real

system. Both controllers in the simulation used a sampling

time of 15 ms. This was done in order to insure that the

sampling time was not impossible to meet.

As mentioned in Table 4, the most significant parameters

were the sampling time, the maximum torque that the motor

can generate and the length to center of mass from the pivot

point. This is reasonable since a longer length to the center of

mass will increase the torque required cancel the gravitational

force. The motor torque is also important to counter the torque

generated by the body itself. It is also reasonable that the sam-

pling time is significant, since even a small change in angle

will have large effect on the necessary torque to counter the

fall and the change in angle should be measured as fast as pos-

sible. Also, the mass of the frame and the radius of the wheel,

seemed less important. This is likely due to the fact that the

mass of the frame is already low, and the same applies to the

length to center of mass. The same applies to the friction coef-

ficient and the mass of the wheel, which both already had low

values. It is important to note that this observation was only

done qualitatively, since the simulation is based on approxima-

tions. The purpose was to observe the trends mentioned above

rather than finding the exact parameters that can be handled.

With this said, it would be recommended to initially lower

the sampling time, increase the maximum torque and dimin-

ish the length to center of mass, before changing anything else.

Comparing the PID parameters in Table 3 with the real

ones, one notices a large difference. This is because of a

number of reasons. One being that the control signal is very

different when comparing Figure 7 with Figure 9, since the

simulation input signal is in ampere and the code for the real

process is the velocity for the wheel. Also, the simulation

inputs angles in radiance, while the real process inputs angles

in degrees. Another reason why the PID parameters differ, is

because the physical parameters differ between the simulation

and the real process. This is true, since the real setup used is

not the same as in Figure 4, which is the structure simulated.

Also, most parameters were identified and can differ from the

real physical parameters.

# 6.3 Tuning the PID controller on the single axis setup

The PID controller was tuned through trial and error with the

help of some intuitive reasoning. Most of the early tuning was

done with only PD-control. Due to the system’s instability

there can be no steady state error, leading us to believe no inte-

gral action should be used. But these ideas proved to be flawed.

Firstly, while it is true that we may want to ease up on

the torque when the pendulum is already on its way up, that

does not mean to lower the control signal. Remember that the

control signal is (roughly) proportional to speed so a lower

control signal actually means decelerating the wheel. If the

wheel decelerates while the pendulum is rising the effect is a torque going the opposite way, sending the pendulum back

down. So a too large KD may hurt the balancing.

Secondly, by introducing integral action | we | can | get the

desired behavior of increasing the speed, which maintains

torque, even when the pendulum is rising. The introduction of

integral action is likely also why the control signal oscillates

around a positive base speed instead of 0. It is then important

to have integral action that reacts quickly, but does not grow

too large. This is why setting Imax | < umax | and adding ref-

erence adjustment eventually led to the best results. Another

advantage of reference adjustment is that it allows the process

to find its own equilibrium. A very interesting example of this

can be found in [4] at 11:25. If there is a discrepancy between

what the IMU registers as 0° and the physical equilibrium,

it could be hard to achieve balance if always controlling to

r = 0. This explains the results seen in Figure 9. The reference

adjustment turned out to be crucial for this reason.

# 6.4 IMU signal

Surprisingly, when measuring the output angle from the IMU

we could not detect any noise at all (Figure 5). Despite this the

raw data readings from the gyrometer were very noisy (Fig-

ure 6). This is problematic if implementing state feedback in

the microcontroller. A good observer would then be needed,

consequently requiring a more accurate model to develop this

observer with the help of simulations. An alternate way of

estimating θ¤
b is of course with a difference quotient, as in

the discretized PID controller. We considered using the gy-

rometer readings as a more accurate estimate of the derivative

even with PID control, but after discovering the noisiness we

decided against it.

# 6.5 Weight reduction

In cases where more time is available, the final design can

be developed through several iterations. For this project, time

was sufficient for designing a single axis setup as a pilot study

for the actual cube. While the thickness of the cube frame

was heavily reduced, compared to the previous prototype, at

points where it could be done, after printing it was concluded

that the thickness could have been reduced even more in order

to save weight. Although, the group is concerned if such a

weight reduction would be enough for the motors to be strong

enough to balance the cube. The components on their own

also contributed to the total weight. With this in mind, even

stronger motors would almost certainly be needed if the cube

is to be driven by a large battery like in this case.

# References

[1] Adafruit. Adafruit motor shield v2 — overview. 2013.

# url: https : / / learn . adafruit . com / adafruit -

motor-shield-v2-for-arduino/overview. (https://learn.adafruit.com/adafruit-motor-shield-v2-for-arduino/overview)

# [2] Adafruit. Adafruit motor shield v2 arduino library. url:

# https : / / adafruit . github . io / Adafruit Motor

Shield V2 Library/html/annotated.html. (https://adafruit.github.io/Adafruit_Motor_Shield_V2_Library/html/annotated.html)

# [3] Arduino. Uno r3 — arduino documentation. url: https:

//docs.arduino.cc/hardware/uno-rev3.

# [4] B. E. Channel. Lego, raspberry and python project -reaction wheel inverted pendulum. 2022. url: https:

//www.youtube.com/watch?v=WObG2LoSEwQ.

[5] M. Gajamohan, M. Merz, I. Thommen, and R. D’Andrea.
The cubli: a cube that can jump up and balance. 2012.

# url: https : / / ethz . ch / content / dam / ethz / special - interest / mavt / dynamic - systems - n -control / idsc - dam / Research DAndrea / Cubli /

Cubli IROS2012.pdf. (https://ethz.ch/content/dam/ethz/special-interest/mavt/dynamic-systems-n-control/idsc-dam/Research_DAndrea/Cubli/Cubli_IROS2012.pdf)

# [6] M. Motors. Gear-motors: series l149. url: https://

# media . distrelec . com / Web / Downloads / 80 / 06 / 05448006.pdf. (https://media.distrelec.com/Web/Downloads/80/06/05448006.pdf)

# [7] ReM-RC. url: https : / / github . com / remrc ? tab = repositories. (https://github.com/remrc?tab=repositories)

# [8] B. Sensortec. Bno055: intelligent 9-axis absolute ori-

entation sensor. 2014. url: https : / / cdn - shop . adafruit . com / datasheets / BST BNO055 DS000 12 .

# pdf. (https://cdn-shop.adafruit.com/datasheets/BST_BNO055_DS000_12.pdf)

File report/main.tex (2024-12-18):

\documentclass[final]{LTHtwocol}
\usepackage[utf8]{inputenc}
\usepackage{graphicx, xcolor}
\usepackage{dsfont}
\usepackage{float}
\usepackage[font=footnotesize]{caption}
\usepackage{subcaption}
\usepackage{amsmath}
\usepackage{amssymb}
\usepackage[export]{adjustbox}
\usepackage{epstopdf}
\usepackage{gensymb}
\usepackage{hyperref}
\usepackage{booktabs}

\hypersetup{
    colorlinks,
    allcolors={blue!40!black}
}
\addbibresource{refs.bib}

\begin{document}
\begin{frontmatter}
\title{Self-balancing cube} 
\author[daniel]{Daniel Holm}
\author[rasmus]{Rasmus Kalvenes}
\author[jonathan]{Jonathan Vesterlund}
\author[gustaf]{Gustaf Waldén}

\email[daniel]{da5838ho-s@student.lu.se}
\email[rasmus]{ra0820ka-s@student.lu.se}
\email[jonathan]{jo2583ve-s@student.lu.se}
\email[gustaf]{gu6615wa-s@student.lu.se}

\advisor[olle]{Olle Kjellqvist}

\begin{abstract}
    The aim of this project was to make a cube balance on an edge, or even a corner if time allows it. This would be done with reaction wheels inside the structure. Besides this, the project also focused on working from a system design perspective, including 3D-printing and selecting electrical components. Using a PID controller with some additions, the group successfully balanced a single axis variant of the problem. A functioning LQG controller was also implemented in simulations of the problem. The learning experience was great. The most significant factors for achieving balance were sampling time, motor strength and pendulum length. A cube structure was created, but could not be made to balance due to time constraints and the factors mentioned.
\end{abstract}

\end{frontmatter}

\section{Introduction}
\input{sec/Introduction}\label{sec:intro}

\section{Physical setups}
\input{sec/SystemSetup}\label{sec:setup}

\section{System dynamics}
\input{sec/Dynamics}\label{sec:dynamics}

\section{Controlling the process}
\input{sec/Control}\label{sec:control}

\section{Results}
\input{sec/Results}\label{sec:results}

\section{Discussion}
\input{sec/Discussion}\label{sec:discussion}

\printbibliography

\end{document}

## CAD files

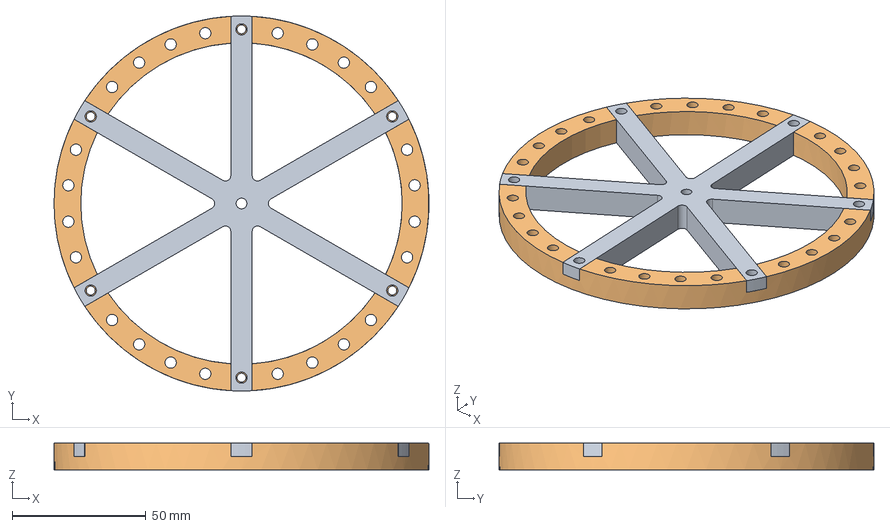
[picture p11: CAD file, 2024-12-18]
schematics/Improved flywheel v6.step
140.0 x 140.0 x 10.0 mm

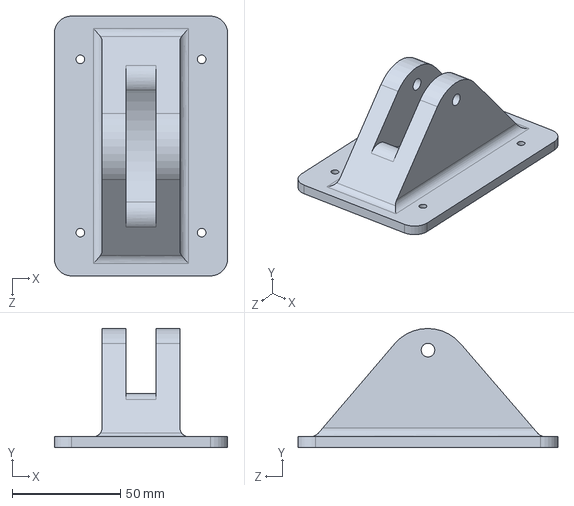
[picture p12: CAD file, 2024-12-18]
schematics/Mounting_Plate.SLDPRT
80.0 x 55.0 x 120.0 mm

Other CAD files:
schematics/Improved flywheel v6.stl

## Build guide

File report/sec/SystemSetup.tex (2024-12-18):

Besides reaction wheels, one for each axis to be balanced around,  there are several other components. One motor to drive each reaction wheel and to control the motors an Arduino UNO R3\cite{arduino} was used. In addition, an Adafruit Motor Shield v2.0\cite{motorshield} was used to control the motors. The shield has the capability to distribute current to the motors of the system from the battery. Combined with Adafruit's library\cite{ms-lib}, the shield uses pulse-width modulation (PWM) to control speed and direction of DC motors. This was needed since it allows for a higher voltage and stronger current than what the Arduino can supply. The microcontroller reads the measurements from an inertial measurement unit (IMU) which calculates the current angle of the system. The IMU used was the BNO055 from Bosch Sensortec\cite{IMU-datasheet} with the help of Adafruit's library\cite{IMU-lib}.

\subsection{Single axis setup}
In order to get a better understanding of reaction wheel balancing a single axis setup was designed and 3D-printed. This setup can be seen in Figure~\ref{fig:SingleAxisV1}. The single axis setup was later modified and improved. The full assembly, including electronic components can be seen in figure \ref{fig:SingleAxisV2}. Despite it being a simple structure, it has the benefit of easy access to port. The microcontroller was not attached to the structure, it laid flat on the table. A prototype build like this allowed us to detect which components are sufficient for the end goal.

\begin{figure}
    \centering
    
    \caption{The first version of the single axis setup}
    \label{fig:SingleAxisV1}
\end{figure}

\begin{figure}
    \centering
    
    \caption{The second version of the single axis setup, with electrical components}
    \label{fig:SingleAxisV2}
\end{figure}

\subsection{The cube}
Designing the structure for the cube proved to be a lot more difficult and time consuming than expected. The intricate design demanded things to be decided based on assumptions, which later turned out to be incorrect. Some parts had to be redesigned multiple times. Some parts, e.g. four sides of the cube, were made identical to make the printing process less difficult. Other parts, engine mounts among them, were made symmetrical for the same reason. An advantage of having multiple identical parts is that if one part fails, it can potentially be replaced by another. While the replacement part is being printed, a side of the cube that is not critical when testing can be relocated into the critical position. The design of the cube can be seen in Figure~\ref{fig:cubediagram} with the parts named in Table~\ref{table:SystemComponents}.

%Här ska jonathans assembly bild in och referera till tabellen nedan.
\begin{figure}
    \centering
    \begin{subfigure}[h]{0.22\textwidth}
        \centering
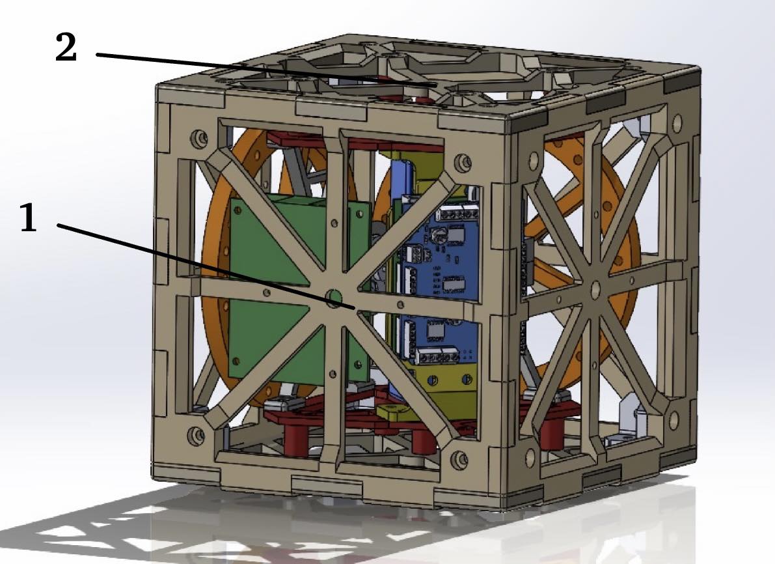
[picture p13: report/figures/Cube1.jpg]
        
    \end{subfigure}
    \begin{subfigure}[h]{0.22\textwidth}
        \centering
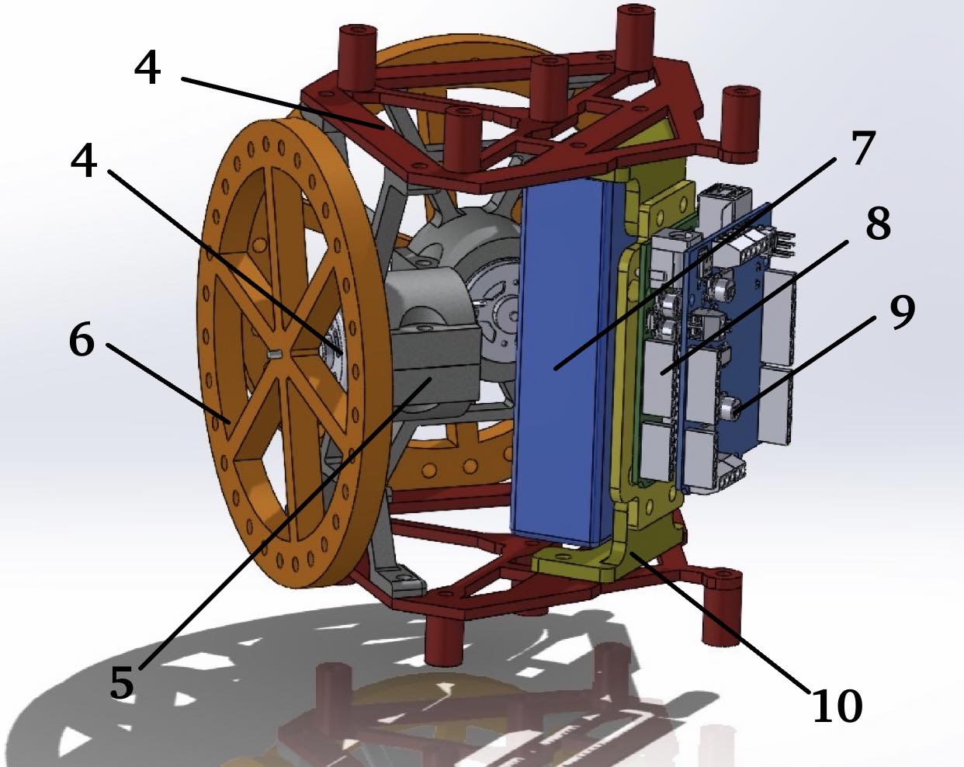
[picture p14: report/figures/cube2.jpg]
        
    \end{subfigure}
    \caption{The components in the system numbered.}
    \label{fig:cubediagram}
\end{figure}

\begin{table}
    \centering
    \begin{tabular}{cc}\toprule
     Component & Number \\\midrule
     Cube, side               & 1\\
     Cube, top and bottom     & 2\\
     Mounting plate           & 3\\
     DC motor                 & 4\\
     Motor holder             & 5\\
     Reaction wheel           & 6\\
     Battery                  & 7\\
     Arduino                  & 8\\
     Arduino Shield           & 9\\
     Electronics holder       & 10\\\bottomrule
    \end{tabular}
    \caption{The components in the system.}
    \label{table:SystemComponents}
\end{table}

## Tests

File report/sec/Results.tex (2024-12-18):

\subsection{Selecting the new motor}
Out of the available off-the-shelf motors the L1491210\cite{motor-datasheet} from Micro Motors was selected. According to \eqref{eq:tau}, it should momentarily hold a tilt angle of $4\degree$, which was more than twice as powerful as the first motor used.

\subsection{Physical parameters}
The physical parameters were identified for the single axis setup. These values were used for the simulations and can be found in Table~\ref{table:MeasuredValues}.

\begin{table}[h]
    \centering
    \begin{tabular}{cc}\toprule
            Parameter  & Value \\\midrule
            $I_{b}$      & $2.1 \cdot 10^{-3} \text{ kg} \cdot \text{m}^2$ \\
            $I_{w}$      & $6.4 \cdot 10^{-3} \text{ kg} \cdot \text{m}^2$ \\
            $m_{b}$      & 0.170 kg \\
            $m_{w}$      & 0.076 kg \\
            $l$            & 0.093 m \\
            $K_{m}$      & 0.5 Nm/A \\
            $T_{\text{max}}$    & 0.015 Nm \\\bottomrule
    \end{tabular}
    \caption{Parameters and their measured values.}
    \label{table:MeasuredValues}
\end{table}

\noindent
The only parameter that was not identified was the friction coefficient, $C_{w}$. Instead, the same value as the one in \cite{cubli-planar} was used, $C_{w} = 5 \cdot 10^{-5} \text{ kg} \cdot \text{m}^2 \cdot \text{s}^{-1}$.

\subsection{Measurements from the IMU}
The structure was tilted slowly from side to side while the angle was measured at 10 ms intervals. The results can be seen in Figure~\ref{fig:imu_angle}.

\begin{figure}[H]
    \centering
    
    \caption{Angle measurements from the IMU.}
    \label{fig:imu_angle}
\end{figure}

\noindent
The structure was then laid still while the angular velocity from the gyrometer was measured at 10 ms intervals. The results can be seen in Figure~\ref{fig:imu_gyro}.

\begin{figure}[H]
    \centering
    
    \caption{Angular velocity measurements from the IMU.}
    \label{fig:imu_gyro}
\end{figure}

\subsection{Simulations}
The model in \eqref{eq:state-space} and \eqref{eq:ss-matrices} was simulated using both a PID controller and a LQG controller. The simulation results can be seen in Figure~\ref{fig:PIDGraph} and Figure~\ref{fig:LQGGraph}. For both simulations, a sample time of 15 ms and a pulse disturbance of $0.5\degree$ was used.
\\\\
The parameter settings for the discrete PID controller can be seen in Table~\ref{table:PIDParameters}.

\begin{table}[H]
    \centering
    \begin{tabular}{cc}\toprule
     Parameter  & Value \\\midrule
     $K_{P}$      & 3\\
     $K_{I}$      & 1\\
     $K_{D}$      & 0.3\\\bottomrule
    \end{tabular}
    \caption{The chosen PID parameters.}
    \label{table:PIDParameters}
\end{table}

\noindent
The optimal gain matrices $K$ and $L$ were calculated as

\begin{equation}
    \begin{gathered}
        K =
        \begin{bmatrix}
            6.0497 & 0.7365 & 0.0611
        \end{bmatrix}
        ,\\
        L = 
        \begin{bmatrix}
            1       & 0\\
            14.0934 & 0.0825\\
            0.8845  & 0.0048\\
        \end{bmatrix}
        .
    \end{gathered}
\end{equation}

\begin{figure}[h]
    \centering
    
    \caption{Simulation of the single axis setup with a disturbance, using the PID controller.}
    \label{fig:PIDGraph}
\end{figure}

\begin{figure}[h]
    \centering
    
    \caption{Simulation of the single axis setup with a disturbance, using the LQG controller. The blue line represents the estimated values and the red dashed line represents the values calculated from the state-space model.}
    \label{fig:LQGGraph}
\end{figure}

\noindent
While experimenting with different parameter settings for the simulation, we observed that some had a larger effect on the system than others. By changing the parameters in the PID simulation, with different factors, the parameters importance could be observed. The observation was based on how high, or low, of a factor a parameter could handle, before the system achieved instability. Sampling time, maximum torque and length to center of mass had the largest effect. This was followed by the mass of the frame and the radius of the wheel. In contrast, the system was still stable with a high friction coefficient and a low mass of the wheel. This qualitative observation is summarized in Table~\ref{table:ParamSig}.

\begin{table}[H]
    \centering
    \begin{tabular}{ccc}\toprule
            Parameter  & Factor & Importance \\\midrule
            $\Delta t$        & 1.2         & Very high\\
            $T_{\text{max}}$  & $2.7^{-1}$  & High\\
            $l$               & 2.8         & High\\
            $m_b$             & 4.5         & Medium\\
            $r_{w}$           & $4.5^{-1}$  & Medium\\
            $m_{w}$           & $< 20^{-1}$ & Low\\
            $C_{w}$           &  40         & Low\\\bottomrule
    \end{tabular}
    \caption{Parameters and their observed importance.}
    \label{table:ParamSig}
\end{table}

\subsection{The physical setup}
The discretized controller from \eqref{eq:PIDdisc} was implemented with a sample time of 10 ms with the original DC motors given to us. The motor was eventually swapped out to the new one\cite{motor-datasheet}. After this, testing could begin again. This time the motor feedback from \eqref{eq:PIDCdisc} was also implemented. Experimenting with PD-control and positive values of $K_C$ seemed promising but balancing still proved difficult. In a last ditch effort a new design for the pendulum body was made. The improved structure can be seen in Figure~\ref{fig:SingleAxisV2}.
\\\\
After some inspiration from\cite{LEGO-video} the controller now made use of integral action with a positive $K_I$ as well as reference adjustment according to \eqref{eq:ref-adjustment}. $K_C$ was now chosen to be negative and relatively small. The idea was to slow down the wheel over time when balancing. After some tuning stable balancing was finally achieved with the following control parameters:

\begin{equation}
    \begin{gathered}
        K_P = 50, \ \ K_I = 150, \ \ K_D = 2.5, \ \ K_C=-0.2, \\
        I_{\text{max}} = 127, \ \ \Delta \theta = 0.004.
    \end{gathered}
\end{equation}

\noindent
Note that the control signal ranges between $\pm255$ (where 255 is simply the max speed of the motor) and the output signal is measured in degrees. The parameter $\Delta \theta$ is also in degrees. In the code implementation, $\Delta t$ was also baked into the constants to reduce the amount of calculations. In Figure~\ref{fig:physical-balance} we can see roughly 15 seconds of balance using the control parameters above. The sensor readings shown are spaced 50 ms apart, but the controller still acted at the usual 10 ms intervals.

\begin{figure}[H]
    \centering
    
    \caption{Top graph: the measured angle $\theta_b$ is in blue and $r$ is in orange. Bottom graph is the control signal.}
    \label{fig:physical-balance}
\end{figure}

\noindent
There are some key takeaways from this graph. Firstly, The structure is not balancing around $0\degree$. Instead, the reference is oscillating slightly around $0.46\degree$. The standard deviation in error over this period was $\sigma_e = 0.24\degree$. Secondly, the control signal is also oscillating around a positive, non-zero speed.
\\\\
Note that these 15 seconds were an excerpt from a longer period of balancing. In reality, the structure could balance for several minutes. The longest measured time balancing was just shy of 37 minutes. It could also handle small disturbances such as shaking the table and gently pushing the structure.

\subsection{The cube}
The physical model can be seen in Figure~\ref{fig:AssembledCube}. The printed parts, structural screws and nuts had a total mass of 587 grams. The scale that was used had an upper limit of 1 kg, which the cube exceeded with the rest of the internal components assembled.

\begin{figure}[H]
    \centering
    \begin{subfigure}[h]{0.2\textwidth}
        \centering
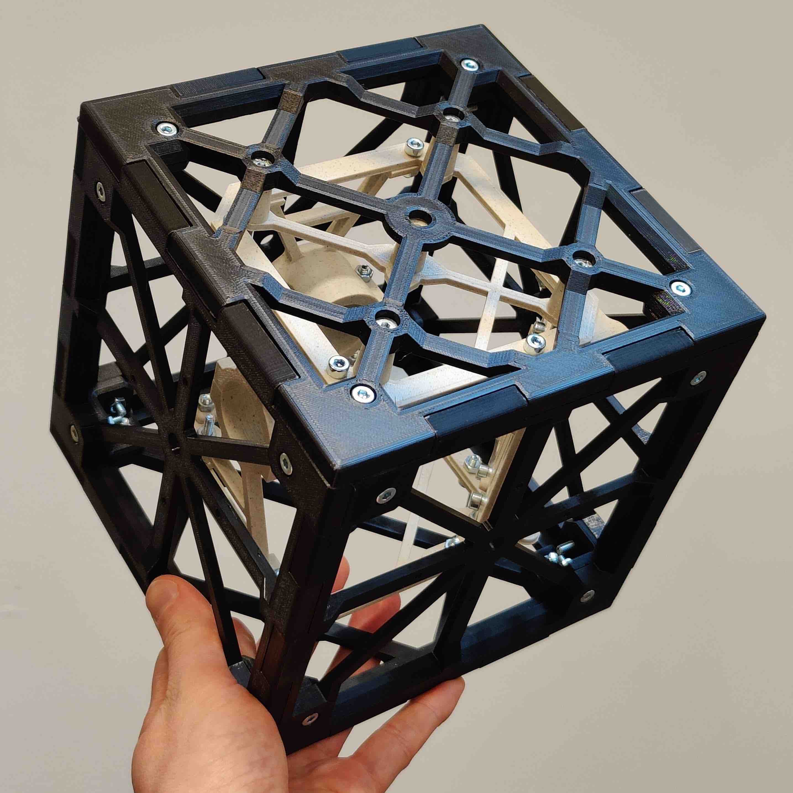
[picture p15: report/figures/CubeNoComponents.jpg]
        
        %\caption{Without electrical components}
        \label{fig:cubeNoComp}
    \end{subfigure}
    \begin{subfigure}[h]{0.2\textwidth}
        \centering
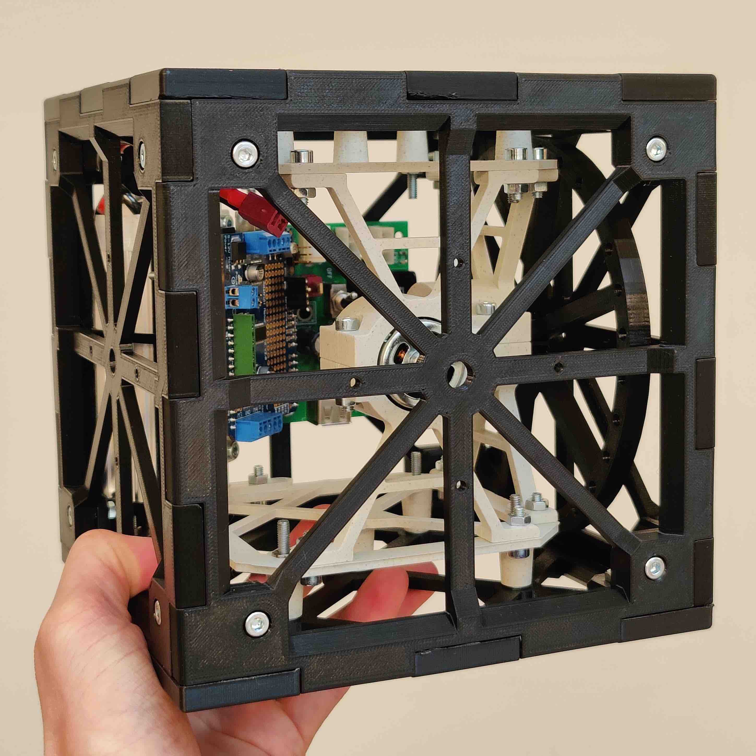
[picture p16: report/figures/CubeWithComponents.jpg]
        
        %\caption{With electrical components}
        \label{fig:cubeWith}
    \end{subfigure}
    \caption{The printed cube with and without components}
    \label{fig:AssembledCube}
\end{figure}

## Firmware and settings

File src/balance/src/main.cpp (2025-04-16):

#include <Arduino.h>
#include <SPI.h>
#include <Wire.h>
#include <Adafruit_MotorShield.h>
#include <Adafruit_MS_PWMServoDriver.h>
#include <Adafruit_Sensor.h>
#include <Adafruit_BNO055.h>
#include <imumaths.h>
#include <functions.h>

/*
	IMU wiring:
		GND to GND - black wire
		5V to 5V - red wire
		SDA to SDA - white wire
		SCL to SCL - orange wire

	Motor wiring:
		+ on motor -(red wire)- Outer port on shield
		Other on motor -(black wire)- Inner port on shield

	Power source: (VERY IMPORTANT)
		Battery or power supply - remove VIn jumper
		12V DC barrel jack - put on VIn jumper
*/

#define MAIN_LOOP_MILLIS 10 // 10 is lower limit for IMU
#define PRINT_LOOP_MILLIS 250 // no need to print every sample
#define SAMPLING_FREQUENCY 100
#define dt 0.01
#define Imax 127 // 127, ~[100 150]

/* Time variables to keep track of loop timings (milliseconds) */
long t, prevPrint, prevLoop;

/* Control variables */
float theta, I, D, controlSignal, error, prevError;

/* Setpoint and gains on startup, best working values so far in comments */
float ref = 0;
float Kp = 45; // 45, ~[45, 55]
float Ki = 120 * dt; // 120, ~[100, 175]
float Kd = 2.5 * SAMPLING_FREQUENCY; // 2.5, ~[2, 3]
float Kc = -0.1; // -0.1, working range is quite wide, ~[-0.4, -0.05]

/* Angle offset obtained from calibration during setup() */
float angleOffset;

/* Create motor shield object with default I2C address */
Adafruit_MotorShield AFMS = Adafruit_MotorShield();

/* Create motor object. Select which 'port' M1, M2, M3 or M4. In this case, M4 */ 
Adafruit_DCMotor *motor = AFMS.getMotor(4);

/* Create IMU object with default I2C adress (default address is 0x29 or 0x28)
									  id, address */
Adafruit_BNO055 bno = Adafruit_BNO055(55, 0x28, &Wire);

void setup() {
	Serial.begin(9600);

	/* Initialize Motor Shield object with the default frequency 1.6KHz */
	if (!AFMS.begin()) {
		Serial.println("Could not find Motor Shield. Check wiring.");
		while(true); // loops forever, reset manually
	}
	Serial.println("Motor Shield found");

	/* Initialize the IMU sensor */
	if(!bno.begin()) {
		Serial.print("Could not find IMU. Check wiring");
		while(true); // loops forever, reset manually
	}
	Serial.println("IMU found");
	bno.setExtCrystalUse(true);

	// turn on motor (is this needed?)
	motor->setSpeed(100); // dummy value
	motor->run(FORWARD);
	motor->run(RELEASE);

	// angleOffset = calibrateOffset();
	// Serial.print("angleOffset = ");
	// Serial.println(angleOffset);

	// printPIDGains();

	// Serial.println("Hit enter to start controller");
	// while (Serial.available() == 0); // waits for user to hit enter
	// Serial.read();
	Serial.flush();
}

void loop() {
	t = millis(); // get current time

	/* Tunes control parameters if there is input from serial */
	// tuning();
	
	/* The controller acts at regular intervals */
	if (t - prevLoop < MAIN_LOOP_MILLIS) return; // skip if not enough time has passed

	/* Get sensor reading for angle */
	theta = degrees(bno.getQuat().toEuler()[1] - angleOffset);
	error = ref - theta;

	/* If pendulum is not close to vertical, do not control */
	if (!isVertical()) {
		motor->run(RELEASE);
		ref = 0;
		I = 0;
		controlSignal = 0;
		prevError = 0;
		prevLoop = t;
		return;
	}

	/* Shifts reference further away by small amount if there is error, can be toggled */
	dither();

	/* Compute integral part and saturate */
	I = constrain(I + error, -Imax, Imax);

	/* Compute derivative estimate */
	D = (error - prevError);

	/* Compute control signal and saturate */
	controlSignal = constrain(Kp * error + Ki * I + Kd * D + Kc * controlSignal, -255, 255);
	
	spinMotor();

	prevError = error;

	/* Print some signals of interest at regular intervals */
	if (t - prevPrint >= PRINT_LOOP_MILLIS) {
		printSignals();
		prevPrint = t;
	}

	prevLoop = t;
}

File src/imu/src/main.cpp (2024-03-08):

#include <Arduino.h>
#include <Wire.h>
#include <SPI.h>
#include <Adafruit_BNO055.h>
#include <Adafruit_Sensor.h>
#include <imumaths.h>

Adafruit_BNO055 bno = Adafruit_BNO055(55, 0x28, &Wire);

/* This program prints out the tilt angle, without offset, or the angular velocity to the serial monitor.
	Press enter when prompted to begin printing values every 10 ms. Stop monitoring when you wish to no longer record.
	These values can then be copied and analyzed in some other program of choice.
*/

/* IMU wiring:
	GND to GND - black wire
	5V to 5V - red wire
	SDA to SDA - white wire
	SCL to SCL - orange wire
*/

void setup() {
	Serial.begin(9600);

	/* Initialise the sensor */
	if(!bno.begin()) {
		Serial.print("Ooops, no BNO055 detected ... Check your wiring or I2C ADDR!");
		while(true); // loops forever, reset manually
	}

	bno.setExtCrystalUse(true);

	Serial.println("Press enter to begin recording");
	while (Serial.available() == 0);
	Serial.read();
	Serial.flush();
}

void loop() {
	/* Uncomment this line to print out tilt angle readings */
	// Serial.println(degrees(bno.getQuat().toEuler()[1]));

	/* Uncomment this line to print out angular velocity readings */
	// Serial.println(degrees(bno.getVector(Adafruit_BNO055::VECTOR_GYROSCOPE).z()));

	delay(10);
}

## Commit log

2024-12-18 Added schematics directory
    [Improved flywheel v6.step, Improved flywheel v6.stl, Mounting_Plate.SLDPRT]
2025-04-16 removed calibration from startup
